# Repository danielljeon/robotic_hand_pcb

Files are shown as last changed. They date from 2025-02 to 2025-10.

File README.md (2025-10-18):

# robotic_hand_pcb



Robotic hand project for actuators/power electronics and sensors/instrumentation
university courses (PCB hardware).

STM32F446RE firmware
repo: [robotic_hand](https://github.com/danielljeon/robotic_hand).

- System architecture is explained in further detail in this software repo.

---

<details markdown="1">
  <summary>Table of Contents</summary>

<!-- TOC -->
* [robotic_hand_pcb](#robotic_hand_pcb)
  * [1 Overview](#1-overview)
  * [2 Board Specifications](#2-board-specifications)
    * [2.1 Connectors](#21-connectors)
      * [2.1.1 BAT+/VIN Terminals](#211-batvin-terminals)
    * [2.2 Switches & Jumpers](#22-switches--jumpers)
    * [2.3 Test Pads](#23-test-pads)
  * [3 Release Notes](#3-release-notes)
    * [3.1 v0.1.0](#31-v010)
    * [3.2 v0.2.0](#32-v020)
  * [4 Development Process](#4-development-process)
    * [4.1 Simulations: OrCAD X (PSpice)](#41-simulations-orcad-x-pspice)
    * [4.2 PCB Design: KiCad](#42-pcb-design-kicad)
    * [4.3 Firmware: CLion and STM32CubeMX](#43-firmware-clion-and-stm32cubemx)
    * [4.4. Version Control: GitHub](#44-version-control-github)
  * [5 Switching Buck Regulator](#5-switching-buck-regulator)
    * [5.1 Load Current Estimation](#51-load-current-estimation)
    * [5.2 Switching Frequency Selection](#52-switching-frequency-selection)
    * [5.3 Inductor Selection](#53-inductor-selection)
    * [5.4 Output Capacitor Selection](#54-output-capacitor-selection)
    * [5.5 Input Capacitor Selection](#55-input-capacitor-selection)
    * [5.6 PSpice Simulation](#56-pspice-simulation)
      * [5.6.1 Schematic](#561-schematic)
      * [5.6.2 Output](#562-output)
      * [5.6.3 Fast Fourier Transform (FFT)](#563-fast-fourier-transform-fft)
  * [💖 Sponsors](#-sponsors)
    * [PCBWay](#pcbway)
      * [Why PCBWay?](#why-pcbway)
<!-- TOC -->

</details>

---

<a href="https://www.pcbway.com">
  PCBWay Logo
</a>

This project is sponsored by **PCBWay**. You can learn more about their valuable
support here: [💖 Sponsors/PCBWay](#pcbway).

---

## 1 Overview

| Hand Assembly Back | Hand Assembly Front |
|:---:|:---:|
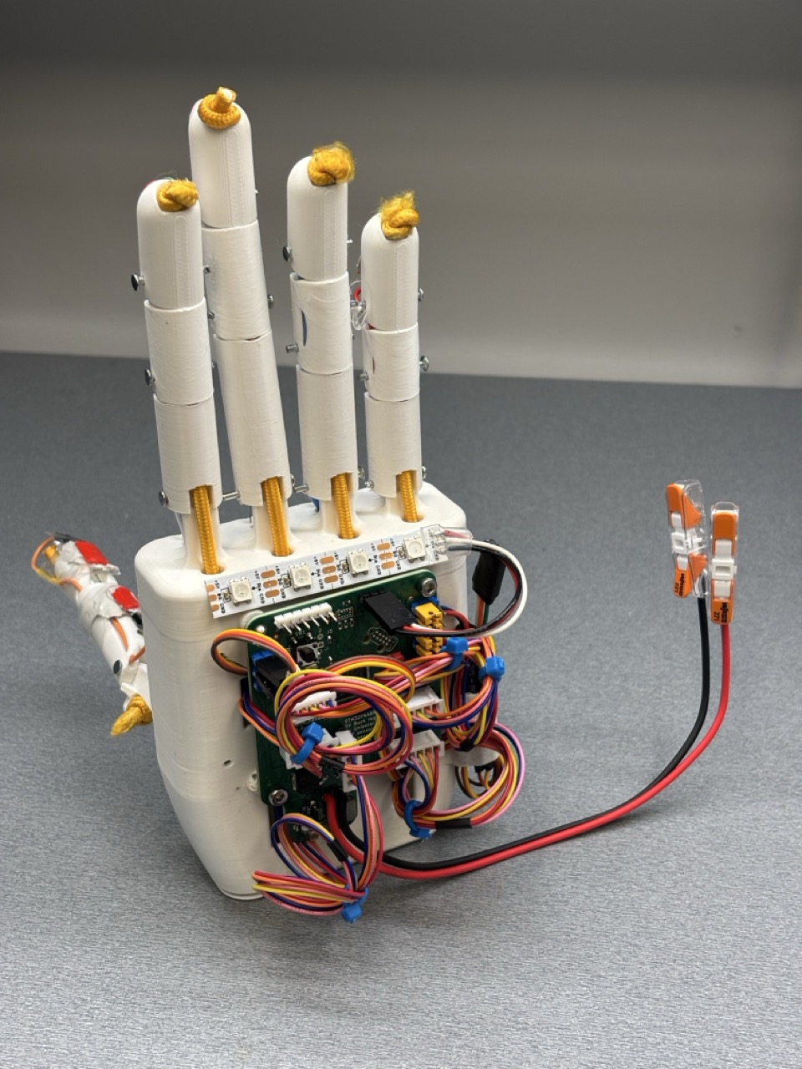
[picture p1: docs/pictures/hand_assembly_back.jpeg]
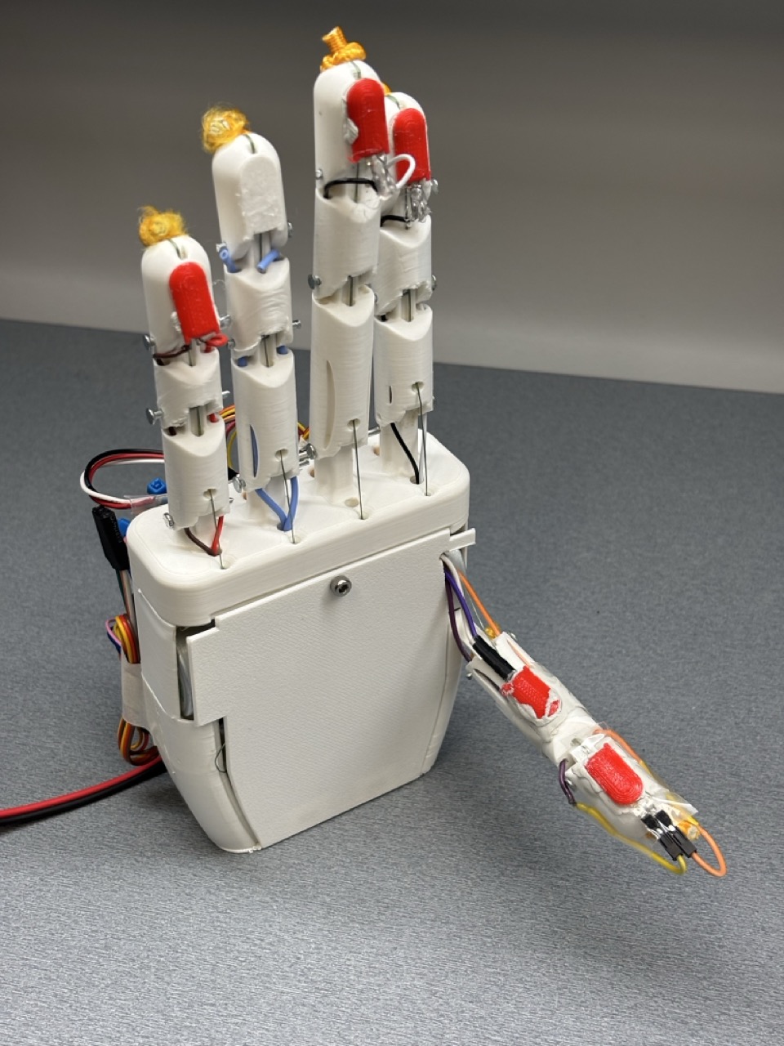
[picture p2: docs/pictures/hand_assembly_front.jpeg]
|  |  |

| Top | Bottom |
|:---:|:---:|
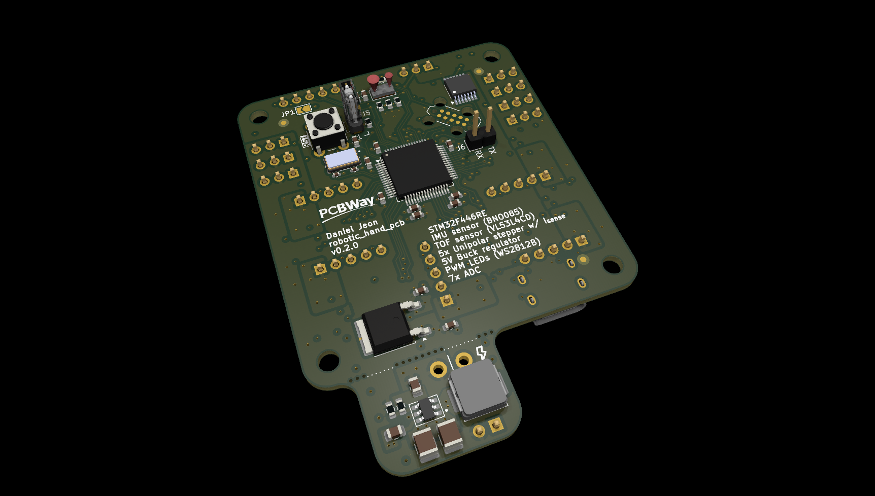
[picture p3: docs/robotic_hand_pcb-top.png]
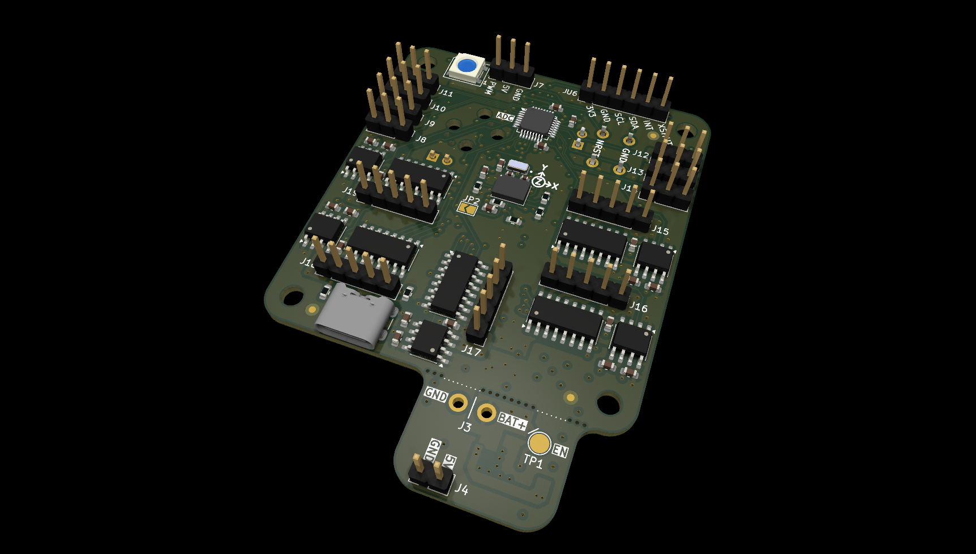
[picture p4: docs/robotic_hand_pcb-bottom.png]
|  |  |
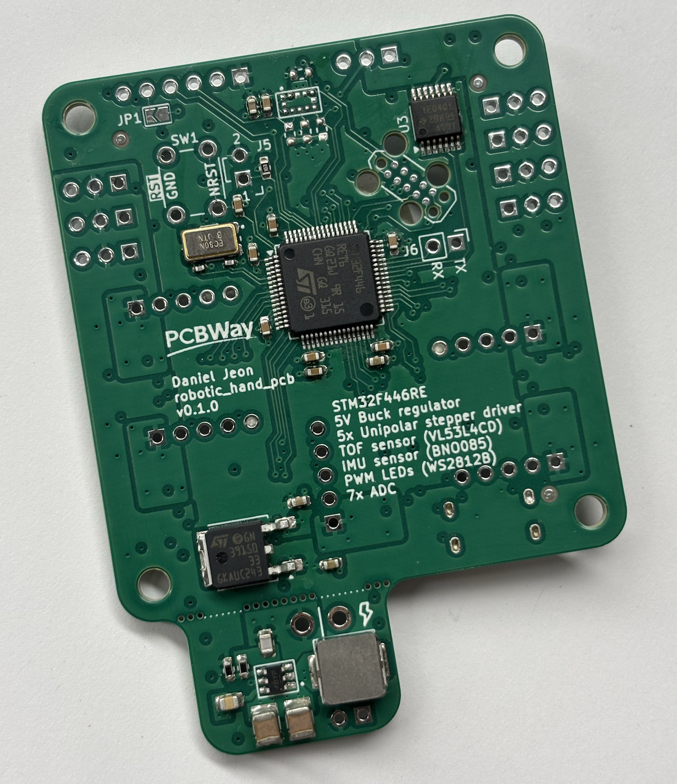
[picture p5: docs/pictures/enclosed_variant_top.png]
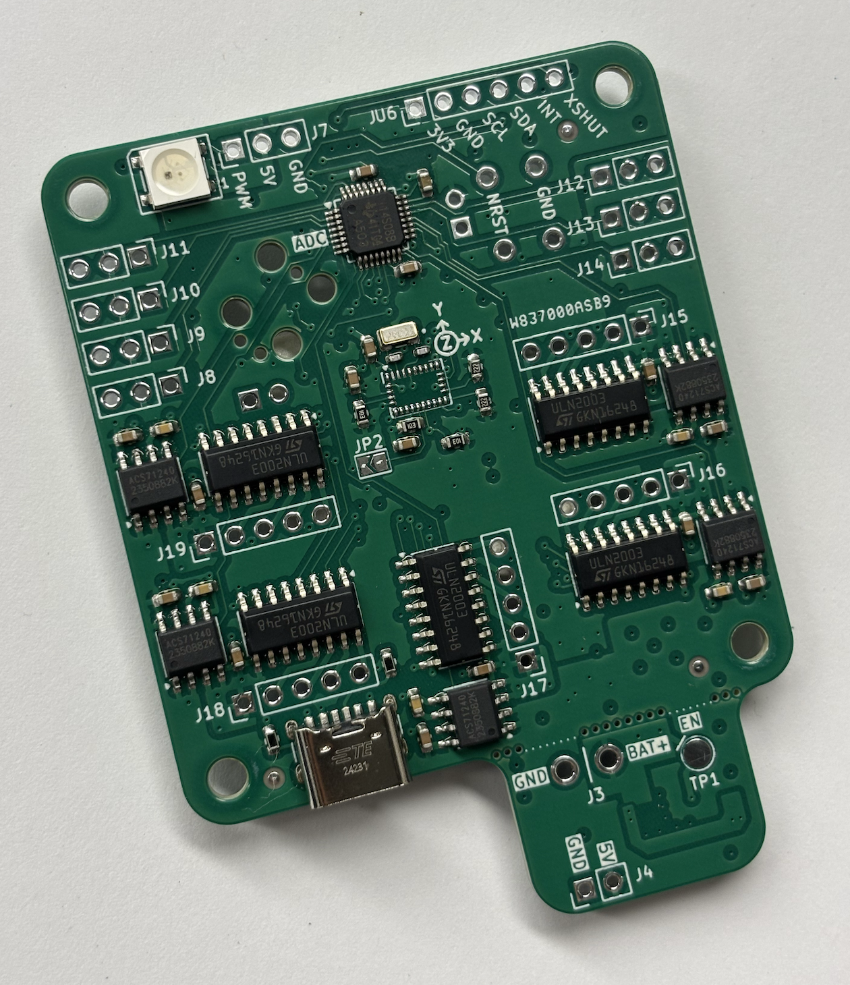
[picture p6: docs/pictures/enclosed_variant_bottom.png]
|  |  |

- Pictures show v0.1.0 production run.

---

## 2 Board Specifications

### 2.1 Connectors

| Connector |  Ref  | Description |
|---|:-----:|---|
| VL53L4CD Breakout  | (J)U6 | Breakout connector for TOF sensor |
| USB-C 5 V power |  J1 | Power only USB-C, primary 5 V source |
| Tag-Connect TC2050 |  J2 | Programming/debug connector |
| BAT+/VIN |  J3 | Pin 1: (GND) Ground, Pin 2: (BAT+) Power supply (> 5 V, <= 36 V), see [2.1.1 BAT+/VIN Terminals](#211-batvin-terminals). |
| 5V Breakout |  J4 | 5 V analog input 7 |
| BOOT0 jumper |  J5 | Open for run flash memory (pull-down on open) |
| UART Breakout |  J6 | General purpose UART breakout |
| WS2812B PWM LEDs |  J7 | 5 V Addressable LED breakout |
| ADC 1 |  J8 | 5 V analog input 1 |
| ADC 2 |  J9 | 5 V analog input 2 |
| ADC 3 |  J10  | 5 V analog input 3 |
| ADC 4 |  J11  | 5 V analog input 4 |
| ADC 5 |  J12  | 5 V analog input 5 |
| ADC 6 |  J13  | 5 V analog input 6 |
| ADC 7 |  J14  | 5 V analog input 7 |
| Unipolar Motor 1 |  J15  | Robotic finger 1 motor |
| Unipolar Motor 2 |  J16  | Robotic finger 2 motor |
| Unipolar Motor 3 |  J17  | Robotic finger 3 motor |
| Unipolar Motor 4 |  J18  | Robotic finger 4 motor |
| Unipolar Motor 5 |  J19  | Robotic finger 5 motor |

- All generic breakout connectors are standard 2.54 mm pitch Harwin connectors
  except for the BAT+/VIN connector.

#### 2.1.1 BAT+/VIN Terminals

The battery or supply terminals for the LMR51430 (5 V) buck regulator are custom
sizes designed for higher gauge wires.

The **recommended supply voltage is 12 V**, however the LMR51430 has a
theoretical range up to 36 volts.

- Hole: 1.5 mm diameter.
- Pad: 2.5 mm diameter.
- Pitch: 4 mm (center-to-center distance).

### 2.2 Switches & Jumpers

| Switch/Jumper | Ref | Description |
|---|:---:|---|
| MCU NRESET switch | SW1 | Generic 6 mm TH button, push to reset |
| VL53L4CD breakout INT | JP1 | Open = no breakout, closed = bridge breakout INT line |
| BNO085 clock select | JP2 | Open = crystal, closed = external/internal |

### 2.3 Test Pads

| Test Pad | Ref | Description |
|---|:---:|---|
| LMR51430 enable | TP1 | Buck converter enable pin (tied to VIN Battery supply by default) |

---

## 3 Release Notes

### 3.1 v0.1.0

- Production oriented 4-layer board variant.
    - Designed for single production run given course project requirement.
- Order date: 2025/02/23.
- Order number: `W837000ASB9`.

### 3.2 v0.2.0

- Updated PCB for hand reworks on `v0.1.0` to get full ADS114S08 feature
  functionality.
    - Requires software changes for this functionality, thus semantic versioning
      minor value was moved to `2`.
    - Rework shown in picture below:
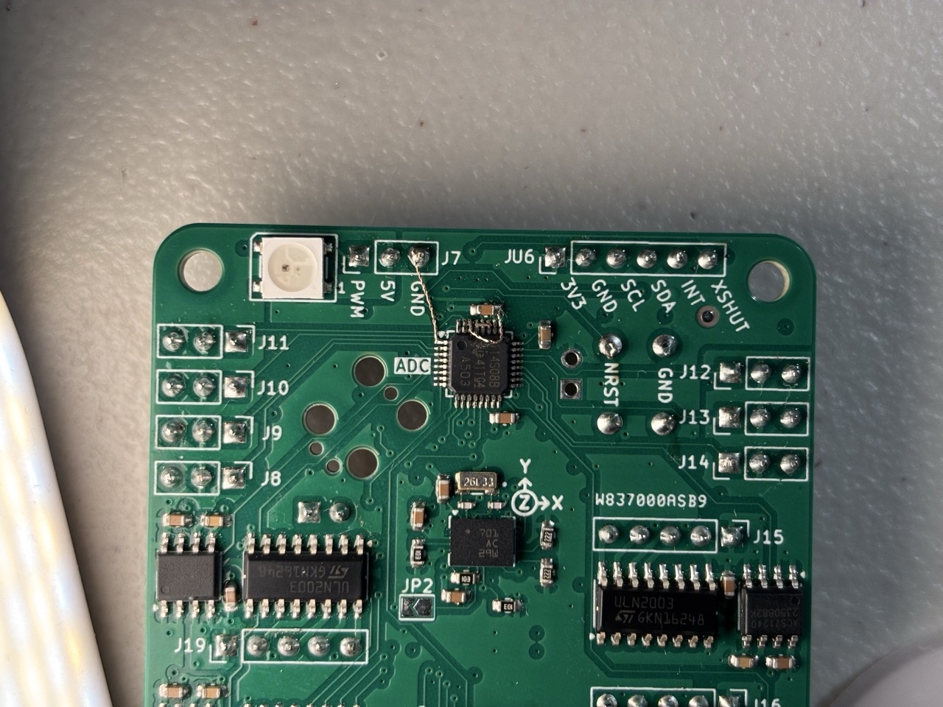
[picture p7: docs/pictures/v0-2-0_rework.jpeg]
      

---

## 4 Development Process

### 4.1 Simulations: OrCAD X (PSpice)

[OrCAD X (PSpice)](https://www.cadence.com/en_US/home/tools/pcb-design-and-analysis/analog-mixed-signal-simulation/pspice.html)
by Cadence was used for circuit simulation and evaluation.

Since this project relies heavily on Texas Instruments (TI) components (ADC ICs,
Darlington transistor arrays, and buck regulators), PSpice was chosen for design
verification and virtual testing. TI provides official PSpice models, making
simulations more accurate and reliable.

Initially, [PSpice for TI](https://www.ti.com/tool/PSPICE-FOR-TI) (a free
version limited to TI parts) was used. Upgrading to OrCAD X enabled full
compatibility and broader simulation capabilities.

### 4.2 PCB Design: KiCad

[KiCad](https://www.kicad.org/) was chosen for PCB design due to its ease of use
as a free, open-source software. Additionally, prior experience and personal
preference played a key role in the decision.

### 4.3 Firmware: CLion and STM32CubeMX

[CLion](https://www.jetbrains.com/clion/)
and [STM32CubeMX](https://www.st.com/en/development-tools/stm32cubemx.html) from
STMicroelectronics were selected based on prior experience and personal
preference. STM32CubeMX is utilized for initial component selection, pin
configuration, and HAL software generation, while CLion is used for general C
firmware development. For more details,
see [robotic_hand](https://github.com/danielljeon/robotic_hand).

### 4.4. Version Control: GitHub

[GitHub](https://github.com/) was chosen for its efficiency in version control
and support for Actions automations. These automations facilitated testing,
validation, and various manufacturing-related processes for both hardware and
software development.

---

## 5 Switching Buck Regulator

The LMR51430 was chosen for its wide input voltage range of 4.5 V to 36 V, high
output current of 3 A and overall efficiency.

> Datasheet: Datasheet: LMR51430 SLUSEF4A – JUNE 2022 – REVISED NOVEMBER 2022.

> Big thanks, as always, to the amazing publicly available resources online 👑:
> 1. [Switching Regulator PCB Design - Phil's Lab #60](https://www.youtube.com/watch?v=AmfLhT5SntE)
> 2. [Switching Regulator Component Selection & Sizing - Phil's Lab #71](https://www.youtube.com/watch?v=FqT_Ofd54fo)

### 5.1 Load Current Estimation

The expected current load is as follows:

| Load | Current | n |
|---|---|---|
| Motors + drivers  | 500 mA  | 5 |
| WS2812B LEDs | 60 mA | 1 |
| 3.3 V ICs via LDO | 100 mA  | 1 |

Approximate total current draw: 2660 mA = 2.66 A at 5 V.

In a real-world engineering scenario, current draw would be estimated using more
accurate models and measured across various revisions of development boards.
However, due to budget constraints and the need to support future higher-voltage
applications, a 3 A buck regulator was chosen, as it is a commonly available and
cost-effective option.

While this provides only an 11% safety margin, it was deemed acceptable for
early research and educational purposes. In the worst-case scenario, the board
can also be powered by an external 5 V power supply if needed.

### 5.2 Switching Frequency Selection

The LMR51430 is capable of 500 kHz and 1.1 MHz switching. The design opted for
the 500 kHz configuration for reduced switching noise and its application of
motor current driving. A lower switching frequency would theoretically reduce
switching losses and improve efficiency at high current draw.

### 5.3 Inductor Selection

The following calculations are based on the recommendations provided in the
LMR51430 datasheet.

The desired peak-to-peak ripple current is given by the following:

$$\Delta i_L = \frac{V_{OUT} \times \left( V_{IN \space MAX} - V_{OUT} \right)}{V_{IN \space MAX} \times L \times f_{SW}}$$

- $L$ = Inductance driving ripple.

The minimum inductor specification is given by:

$$L_{min} = \frac{V_{\text{IN MAX}} - V_{\text{OUT}}}{I_{\text{OUT}} \times K_{\text{IND}}} \times \frac{V_{\text{OUT}}}{V_{\text{IN MAX}} \times f_{\text{SW}}}$$
$$L_{min} = \frac{12 \space \text{V} - 5 \space \text{V}}{3 \space \text{A} \times 0.3} \times \frac{5 \space \text{V}}{12 \space \text{V} \times 500 \times 10^{3} \space \text{Hz}}$$
$$L_{min} = 6.84 \times 10^{-6} \space \text{H} = 6.84 \space \mathrm{\mu H}$$

- $K_{IND}$ = Coefficient representing the inductor ripple current as a fraction
  of the maximum output current, utilizing 0.3 for this project.
    - > A reasonable value of KIND must be 20% to 60% of maximum IOUT supported
      > by the converter.
      >
      > - Datasheet section: _9.2.2.4 Inductor Selection_.
- $f_{\text{SW}}$ = Switching frequency, 500 kHz chosen.
- $V_{\text{IN MAX}}$ = Input voltage, expected 12 V with ±1 V, 13 V.
- $V_{\text{OUT}}$ = Output voltage, 5 V.
- $I_{\text{OUT}}$ = Output current, approximately 3 A.

> During an instantaneous over-current operation event, the RMS and peak
> inductor current can be high. The inductor saturation current must be higher
> than peak current limit level.
>
> In general, choose lower inductance in switching power supplies because it
> usually corresponds to faster transient response, smaller DCR, and reduced
> size for more compact designs. Too low of an inductance can generate too large
> of an inductor current ripple such that over-current protection at the full
> load can be falsely triggered and generates more inductor core loss because
> the current ripple is larger. Larger inductor current ripple also implies
> larger output voltage ripple with the same output capacitors. With peak
> current mode control,ensure there is an adequate amount of inductor ripple
> current. A larger inductor ripple current improves the comparator
> signal-to-noise ratio.
>
> - Datasheet section: _9.2.2.4 Inductor Selection_.

The final minimum inductance value of 6.84 μH closely matches the example
application values provided for a 12V input and 5V output, which uses 6.8 μH.

### 5.4 Output Capacitor Selection

> Minimize the output capacitance to keep cost and size down. The output
> capacitor or capacitors, COUT, must be chosen with care because it directly
> affects the steady state output voltage ripple, loop stability, and output
> voltage overshoot and undershoot during load current transient. The output
> voltage ripple is essentially composed of two parts. One part is caused by the
> inductor ripple current flowing through the Equivalent Series Resistance (ESR)
> of the output capacitors ... The other part is caused by the inductor current
> ripple charging and discharging the output capacitors.
>
> - Datasheet section: _9.2.2.5 Output Capacitor Selection_.

Inductor current ripple flowing through the ESR is given by:

$$\Delta V_{\text{OUT ESR}} = \Delta i_L \times \text{ESR} = K_{\text{IND}} \times I_{\text{OUT}} \times \text{ESR}$$

Inductor current ripple charging and discharging the output capacitors is given
by:

$$\Delta V_{\text{OUT C}} = \frac{\Delta i_L}{8 \times f_{\text{SW}} \times C_{\text{OUT}}} = \frac{K_{\text{IND}} \times I_{\text{OUT}}}{8 \times f_{\text{SW}} \times C_{\text{OUT}}}$$

- $K_{\text{IND}}$ = target ripple ratio of the inductor
  current ($\Delta i L / I_{\text{OUT}}$).

The minimum output capacitance needed for a specified output voltage overshoot
and undershoot is given by:

$$C_{\text{OUT}} > \frac{1}{2} \times \frac{8 \times (I_{\text{OH}} - I_{\text{OL}})}{f_{\text{SW}} \times \Delta V_{\text{OUT SHOOT}}}$$

- $I_{\text{OL}}$ = low level output current during load transient.
- $I_{\text{OH}}$ = high level output current during load transient.
- $V_{\text{OUT SHOOT}}$ = target output voltage overshoot or undershoot.

For this project a target output ripple is arbitrarily set for 30 mV and the
ripple ratio of inductor current is set to 0.3.

- $\Delta V_{\text{OUT ESR}} = \Delta V_{\text{OUT C}} = 30 mV$
- $K_{\text{IND}} = 0.3$

This yields ESR < 75 mΩ and output capacitance > 14 μF.

### 5.5 Input Capacitor Selection

> The LMR51430 device requires a high frequency input decoupling capacitor or
> capacitor. The typical recommended value for the high frequency decoupling
> capacitor is 4.7 μF or higher. TI recommends a high-quality ceramic type X5R
> or X7R with a sufficient voltage rating. The voltage rating must be greater
> than the maximum input voltage. To compensate the derating of ceramic
> capacitors, TI recommends a voltage rating of twice the maximum input voltage.
>
> - Datasheet section: _9.2.2.5 Output Capacitor Selection_.

### 5.6 PSpice Simulation

Due to the limited availability of publicly accessible PSpice models, the
LMR51420 model was used instead. Based on datasheet specifications, the 2A
variant of the LMR514x0 series appears largely similar, with the primary
difference being the requirement for a 10 μH inductor.

#### 5.6.1 Schematic

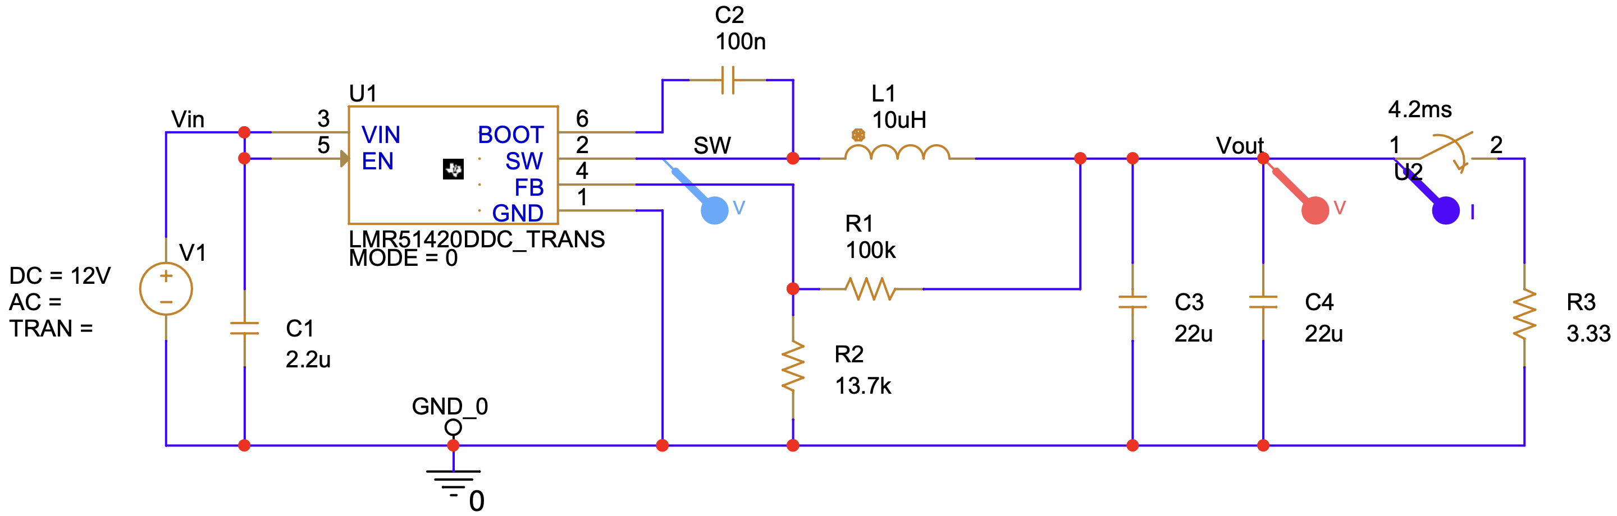
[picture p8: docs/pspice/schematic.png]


To simulate sudden current loads, a 3.3 Ω load (drawing 1.5 A at 5 V) is added
and set to switch at 4.2 ms. The switch has a transition time of 15 μs.

#### 5.6.2 Output

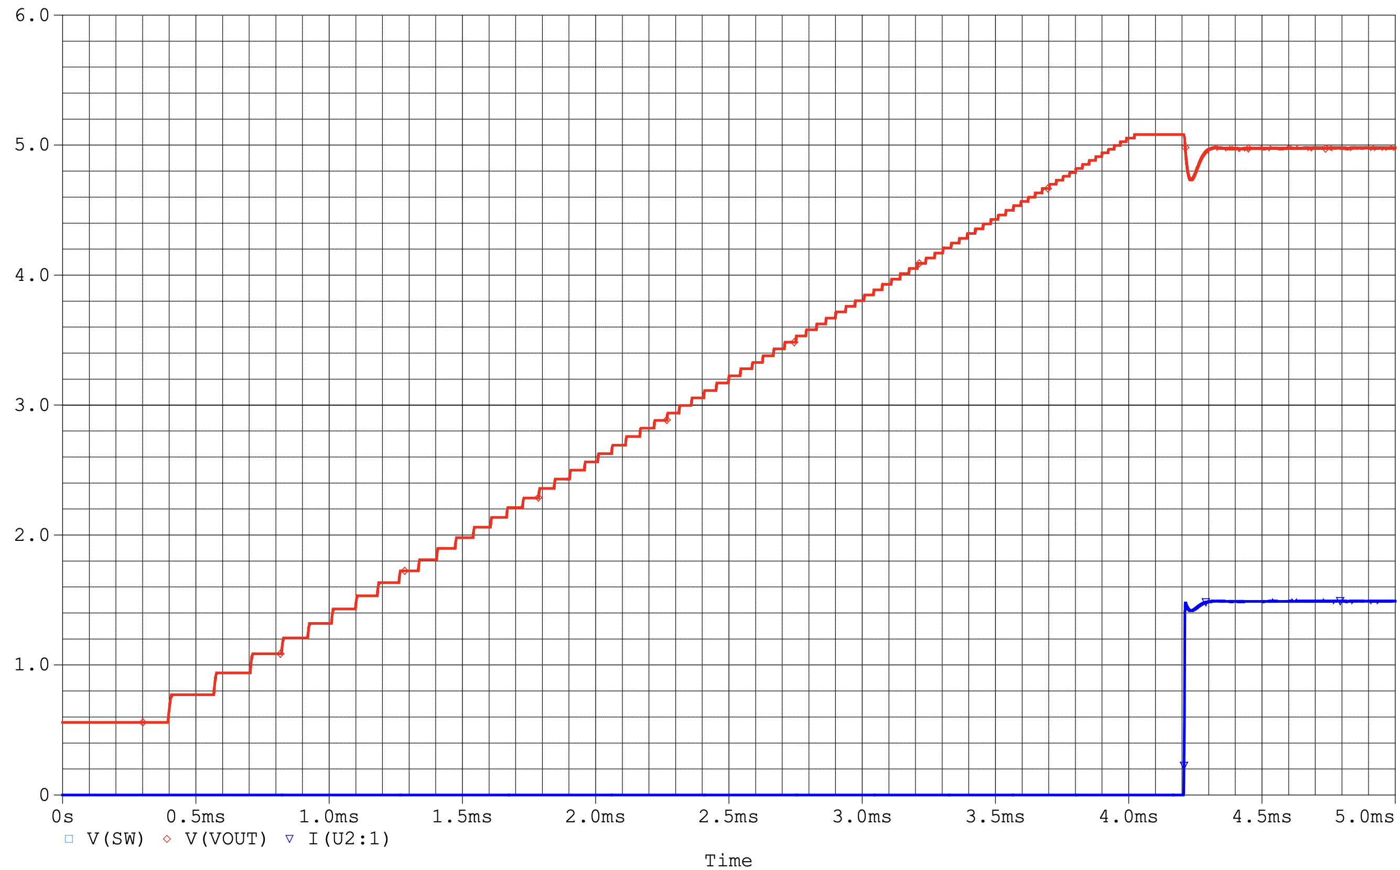
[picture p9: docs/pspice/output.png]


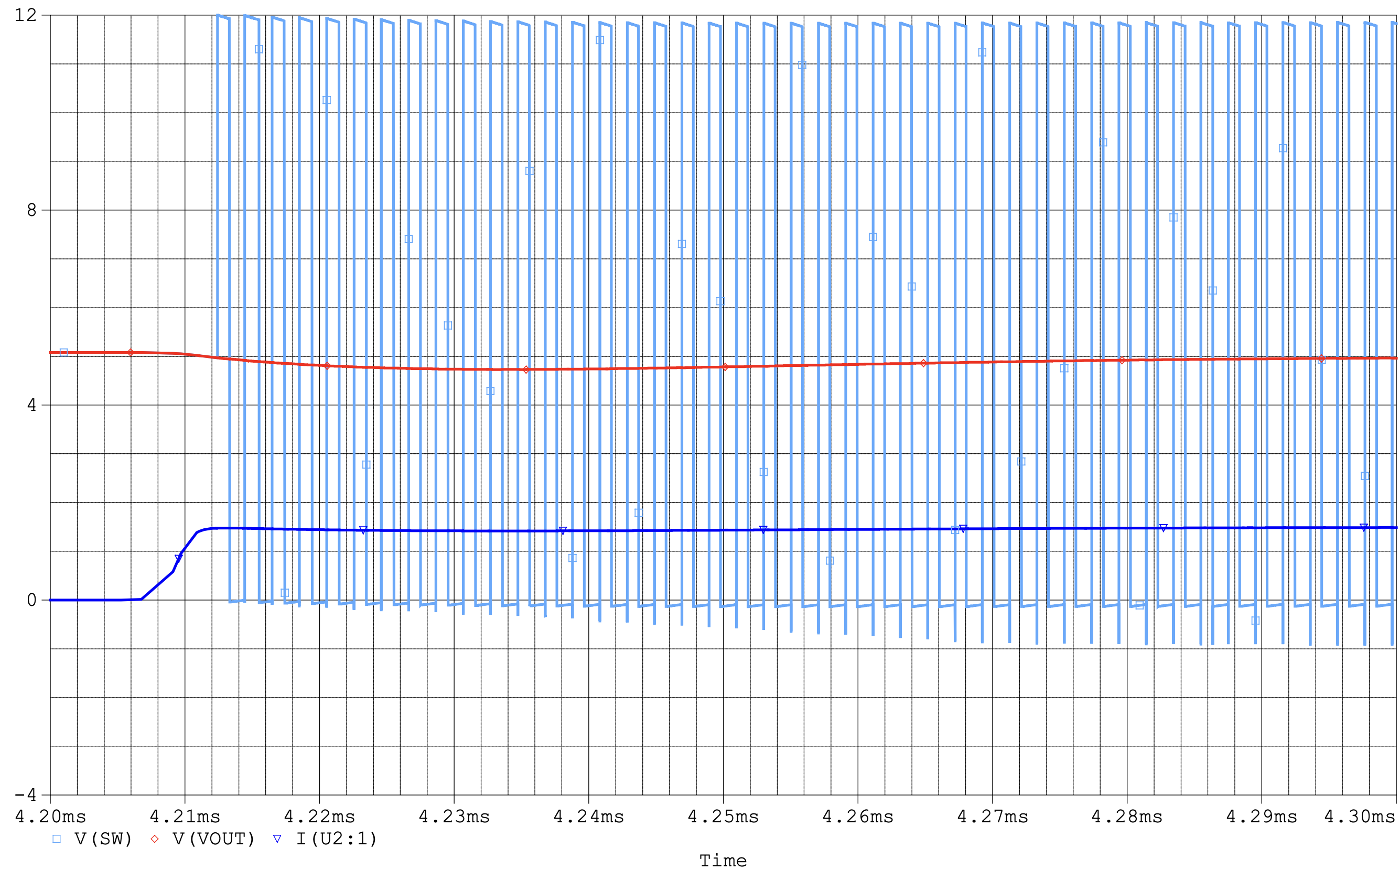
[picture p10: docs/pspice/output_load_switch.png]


#### 5.6.3 Fast Fourier Transform (FFT)

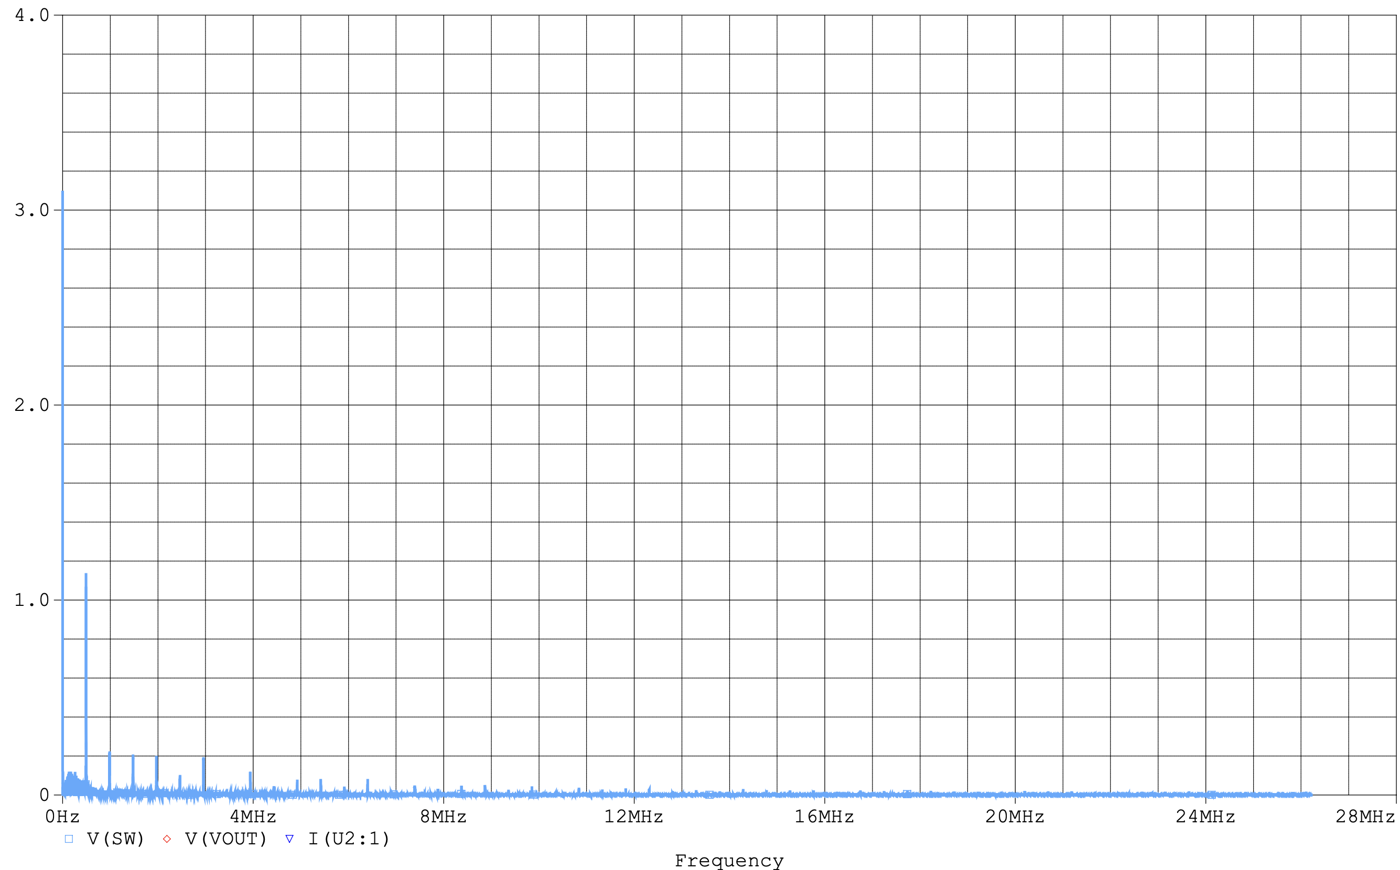
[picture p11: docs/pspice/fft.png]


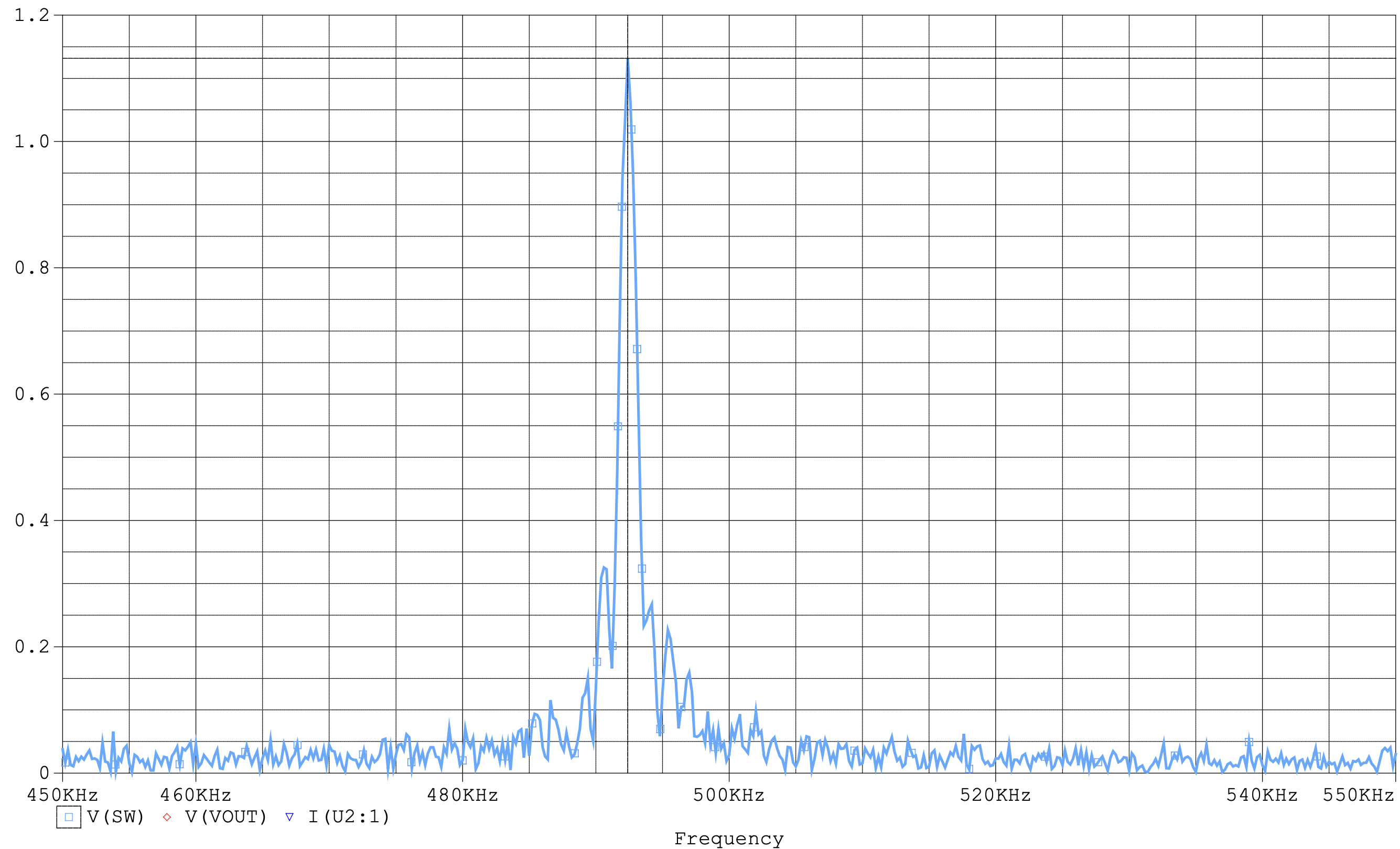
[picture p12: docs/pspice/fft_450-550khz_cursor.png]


For this simulation run, the fundamental frequency was found to be 492.400 kHz
with a resultant amplitude of 1.1316. Due to the short simulation duration, the
time required to ramp up to the final voltage, and the handling of sudden loads,
it is hypothesized that the FFT results deviate slightly from the expected 500
kHz.

---

## 💖 Sponsors

### PCBWay

<a href="https://www.pcbway.com">
  PCBWay Logo
</a>

This project is sponsored by [**PCBWay**](https://www.pcbway.com), whose PCB
manufacturing services are essential in producing high-quality prototypes for
its development. Their support ensures reliable boards that meet the project's
demands.

#### Why PCBWay?

PCBWay stands out for their exceptional services and commitment to the
community:

- **PCB Manufacturing**: High-quality fabrication with options for multilayer,
  rigid-flex, and advanced designs.
- **PCB Assembly**: Comprehensive solutions, including soldering, component
  sourcing, and assembly.
- **CNC Machining & 3D Printing**: Additional prototyping options to support
  complete product development.
- **Fast Turnaround**: Reliable and quick production times to keep projects on
  schedule.
- **Support for Open Source & Education**: PCBWay actively sponsors projects and
  provides educational resources like tutorials, videos, and documentation,
  empowering developers and hobbyists.
    - This commitment to education and open-source advocacy was a key factor in
      choosing them as a partner 🙂.

Their dedication to professional-grade services and fostering innovation makes
PCBWay an invaluable partner in bringing this project to life.

Learn more here: [Why PCBWay?](https://www.pcbway.com/why.html)

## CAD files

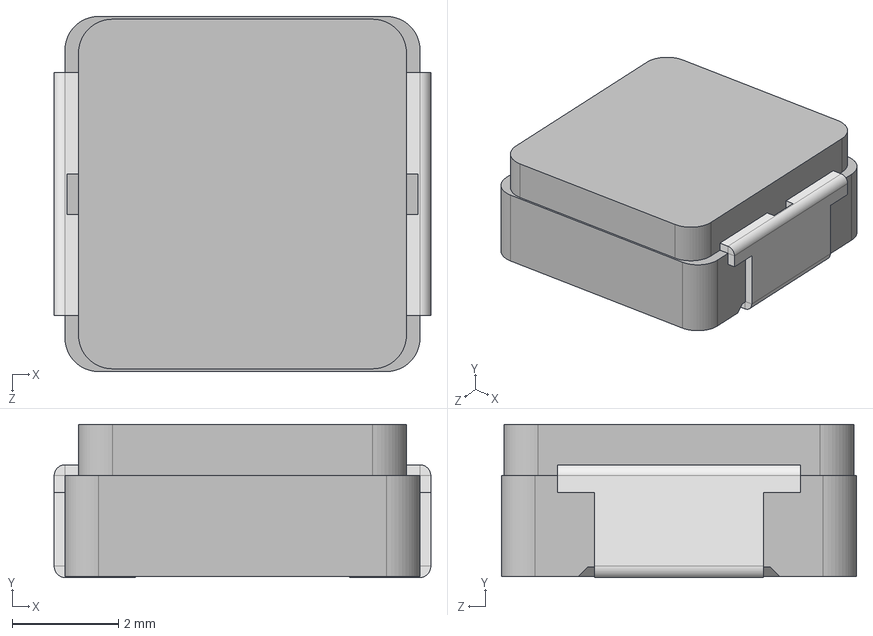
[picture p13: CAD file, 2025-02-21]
component_local/model_3d/IHLP2525CZ.step
7.08 x 2.88 x 6.67 mm

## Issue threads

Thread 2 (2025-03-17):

ADS114S08 missing smoothing resistors

danielljeon, 2025-03-17:
# ADS114S08 missing smoothing resistors

The current ADS114S08 schematic fails to meet datasheet recommendations "**10.1.1 Serial Interface Connections**".

> "Place 47-Ω resistors in series with all digital input and output pins (CS, SCLK, DIN, DOUT/DRDY, and DRDY). This resistance smooths sharp transitions, suppresses overshoot, and offers some overvoltage protection. Care must be taken to meet all SPI timing requirements because the additional resistors interact with the bus capacitances present on the digital signal lines."

47 Ω resistors should be in series with the following:

1. RESET_N
2. DRDY_N
3. DOUT/DRDY_N
4. SCLK
5. DIN
6. CS
7. START/SYNC

This PCB was originally intended for a single production run, so it is unlikely to be directly resolved beyond documentation. Future designs should address and correct this issue.

A note has been left on the schematic to document the known issue.

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

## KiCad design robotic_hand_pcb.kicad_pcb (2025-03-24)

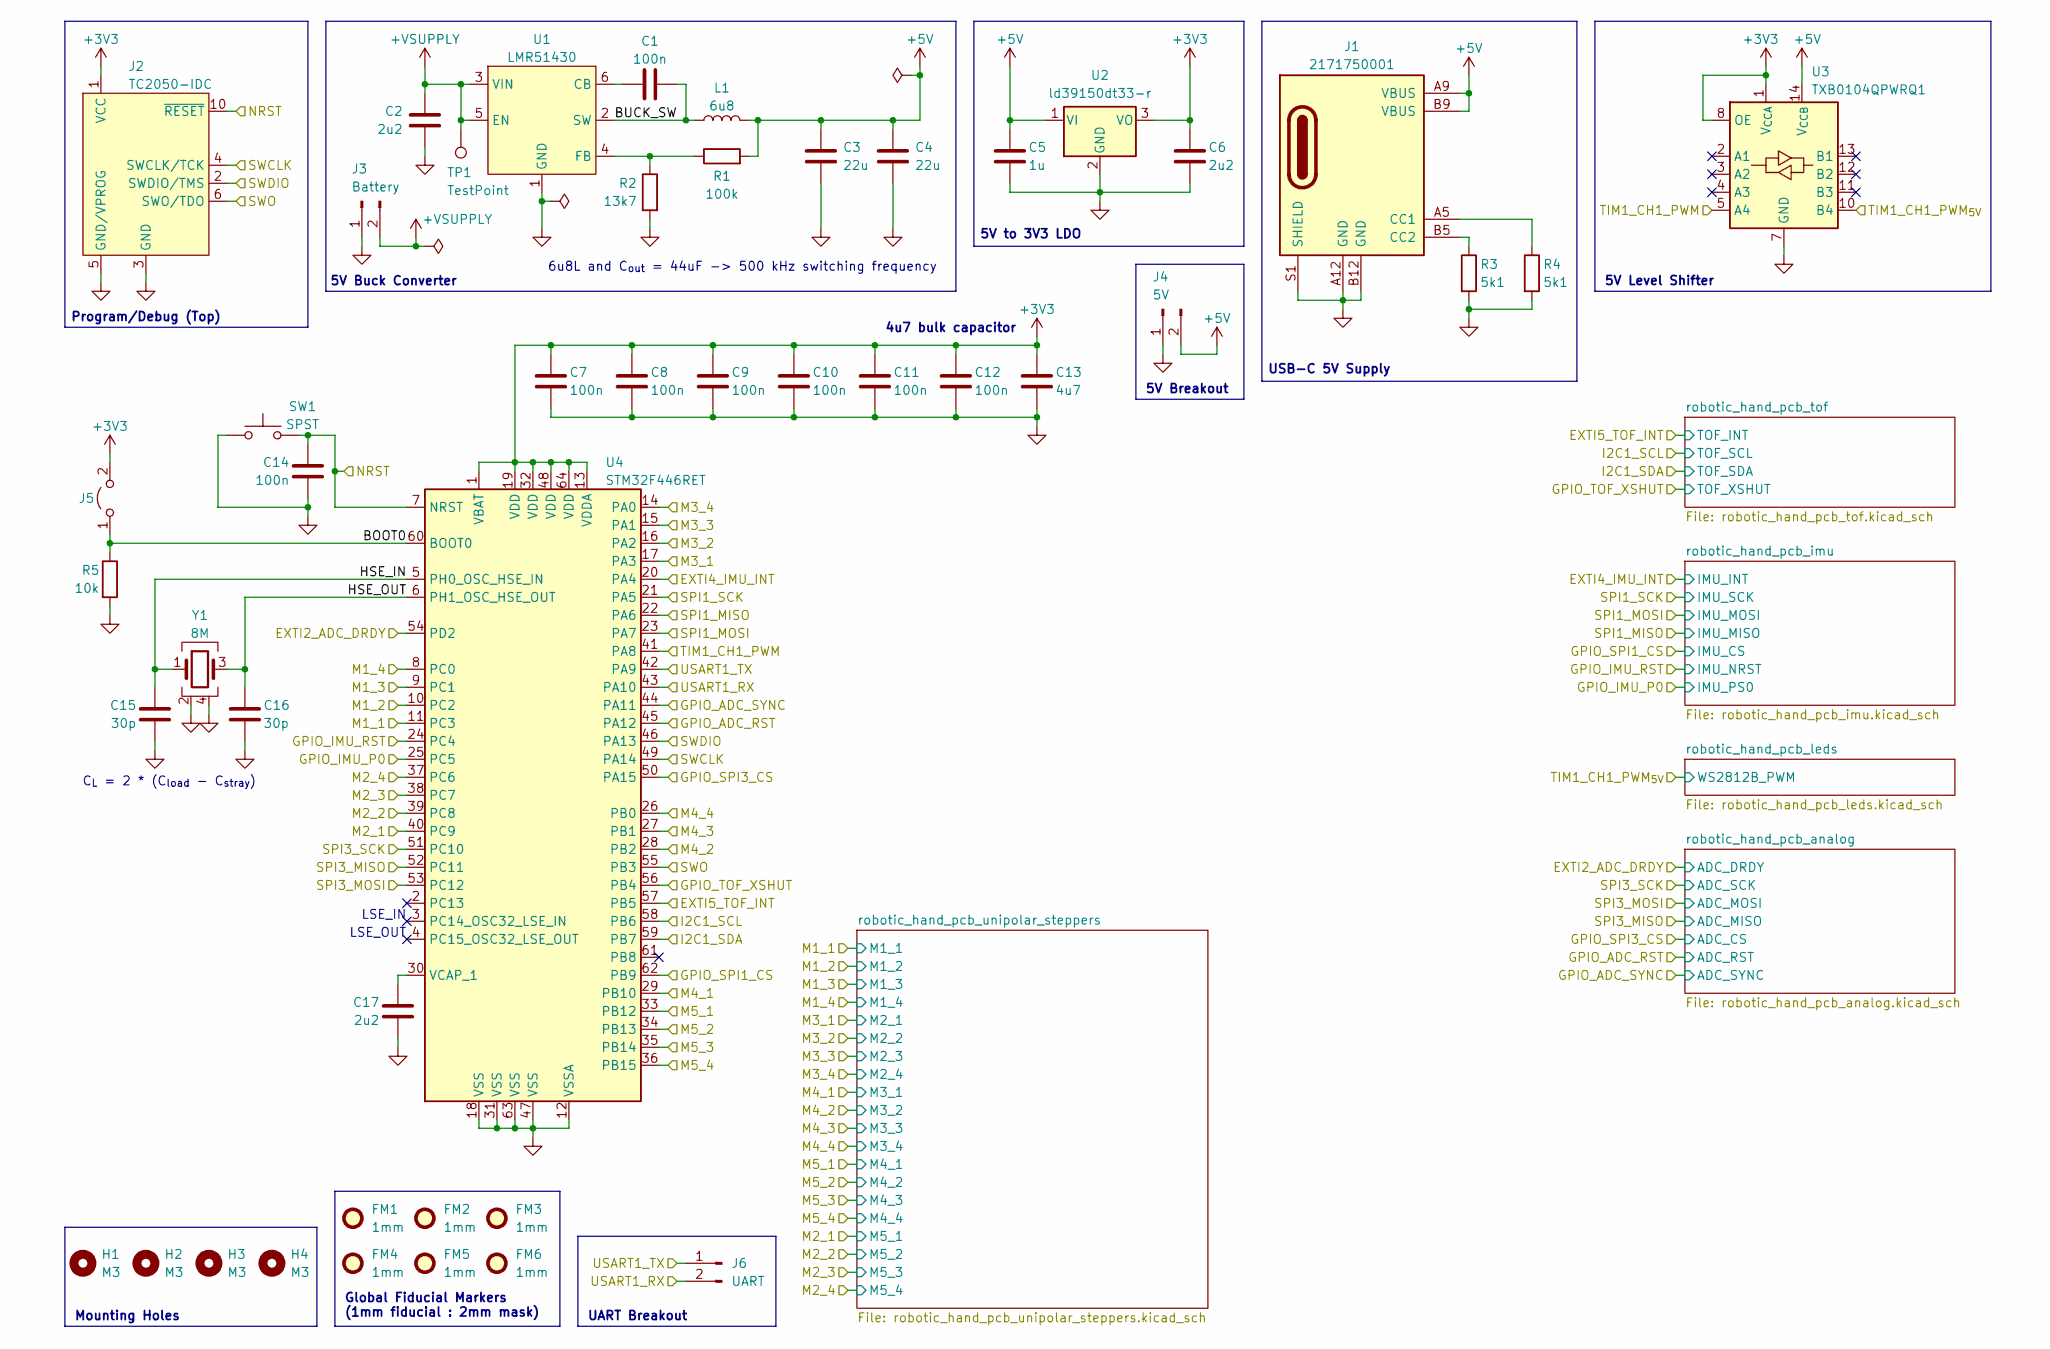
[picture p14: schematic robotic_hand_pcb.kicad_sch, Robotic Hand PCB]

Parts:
C1: 100n; C_0805_2012Metric
C2: 2u2; C_0805_2012Metric
C3, C4: 22u; C_1210_3225Metric
C5: 1u; C_0603_1608Metric
C6, C17: 2u2; C_0603_1608Metric
C7, C8, C9, C10, C11, C12, C14: 100n; C_0603_1608Metric
C13: 4u7; C_0603_1608Metric
C15, C16: 30p; C_0402_1005Metric
FM1, FM2, FM3, FM4, FM5, FM6: 1mm; Fiducial_1mm_Mask2mm
H1, H2, H3, H4: M3; MountingHole_3.2mm_M3
J1: 2171750001; molex_2171750001_usb_c_6p; Manufacturer Part Number 2171750001
J2: TC2050-IDC; tag_connect_tc2050-idc; Manufacturer Part Number TC2050-IDC
J3: Battery; battery
J4: 5V; PinHeader_1x02_P2.54mm_Vertical
J5: harwin_2p_2-54_jumper_open; Manufacturer Part Number M20-9990246
J6: UART; PinHeader_1x02_P2.54mm_Vertical
L1: 6u8; vishay_ihlp-2525cz
R1: 100k; R_0603_1608Metric
R2: 13k7; R_0603_1608Metric
R3, R4: 5k1; R_0603_1608Metric
R5: 10k; R_0603_1608Metric
SW1: SPST; SW_PUSH_6mm
TP1: TestPoint; TestPoint_Pad_D2.5mm
U1: LMR51430; lmr51430; Manufacturer Part Number LMR51430
U2: ld39150dt33-r; to-252-2_dpak-2-leg; Manufacturer Part Number LD39150DT33-R
U3: TXB0104QPWRQ1; txb0104qpwrq1; Manufacturer Part Number TXB0104QPWRQ1
U4: STM32F446RET; LQFP-64_10x10mm_P0.5mm; Manufacturer Part Number STM32F446RE
Y1: 8M; ecs_ecx-64; Manufacturer Part Number ECS-80-18-23B-JTN-TR

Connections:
+3V3: C6.1, C7.1, C8.1, C9.1, C10.1, C11.1, C12.1, C13.1, J2.1 (VCC), J5.2, U2.3 (VO), U3.1 (V_{CCA}), U3.8 (OE), U4.1 (VBAT), U4.13 (VDDA), U4.19 (VDD), U4.32 (VDD), U4.48 (VDD), U4.64 (VDD); also elsewhere on the board
+5V: C3.2, C4.2, C5.1, J1.A9 (VBUS), J1.B9 (VBUS), J4.2, L1.2, R1.2, U2.1 (VI), U3.14 (V_{CCB}); also elsewhere on the board
+VSUPPLY: C2.1, J3.2, TP1.1, U1.3 (VIN), U1.5 (EN)
/BOOT0: J5.1, R5.1, U4.60 (BOOT0)
/BUCK_SW: C1.2, L1.1, U1.2 (SW)
/EXTI2_ADC_DRDY: U4.54 (PD2); also elsewhere on the board
/EXTI4_IMU_INT: U4.20 (PA4); also elsewhere on the board
/EXTI5_TOF_INT: U4.57 (PB5); also elsewhere on the board
/GPIO_ADC_RST: U4.45 (PA12); also elsewhere on the board
/GPIO_ADC_SYNC: U4.44 (PA11); also elsewhere on the board
/GPIO_IMU_P0: U4.25 (PC5); also elsewhere on the board
/GPIO_IMU_RST: U4.24 (PC4); also elsewhere on the board
/GPIO_SPI1_CS: U4.62 (PB9); also elsewhere on the board
/GPIO_SPI3_CS: U4.50 (PA15); also elsewhere on the board
/GPIO_TOF_XSHUT: U4.56 (PB4); also elsewhere on the board
/HSE_IN: C15.1, U4.5 (PH0_OSC_HSE_IN), Y1.1
/HSE_OUT: C16.1, U4.6 (PH1_OSC_HSE_OUT), Y1.3
/I2C1_SCL: U4.58 (PB6); also elsewhere on the board
/I2C1_SDA: U4.59 (PB7); also elsewhere on the board
/M1_1: U4.11 (PC3); also elsewhere on the board
/M1_2: U4.10 (PC2); also elsewhere on the board
/M1_3: U4.9 (PC1); also elsewhere on the board
/M1_4: U4.8 (PC0); also elsewhere on the board
/M2_1: U4.40 (PC9); also elsewhere on the board
/M2_2: U4.39 (PC8); also elsewhere on the board
/M2_3: U4.38 (PC7); also elsewhere on the board
/M2_4: U4.37 (PC6); also elsewhere on the board
/M3_1: U4.17 (PA3); also elsewhere on the board
/M3_2: U4.16 (PA2); also elsewhere on the board
/M3_3: U4.15 (PA1); also elsewhere on the board
/M3_4: U4.14 (PA0); also elsewhere on the board
/M4_1: U4.29 (PB10); also elsewhere on the board
/M4_2: U4.28 (PB2); also elsewhere on the board
/M4_3: U4.27 (PB1); also elsewhere on the board
/M4_4: U4.26 (PB0); also elsewhere on the board
/M5_1: U4.33 (PB12); also elsewhere on the board
/M5_2: U4.34 (PB13); also elsewhere on the board
/M5_3: U4.35 (PB14); also elsewhere on the board
/M5_4: U4.36 (PB15); also elsewhere on the board
/NRST: C14.2, J2.10 (~RESET), SW1.2, U4.7 (NRST)
/SPI1_MISO: U4.22 (PA6); also elsewhere on the board
/SPI1_MOSI: U4.23 (PA7); also elsewhere on the board
/SPI1_SCK: U4.21 (PA5); also elsewhere on the board
/SPI3_MISO: U4.52 (PC11); also elsewhere on the board
/SPI3_MOSI: U4.53 (PC12); also elsewhere on the board
/SPI3_SCK: U4.51 (PC10); also elsewhere on the board
/SWCLK: J2.4 (SWCLK/TCK), U4.49 (PA14)
/SWDIO: J2.2 (SWDIO/TMS), U4.46 (PA13)
/SWO: J2.6 (SWO/TDO), U4.55 (PB3)
/TIM1_CH1_PWM: U3.5 (A4), U4.41 (PA8)
/TIM1_CH1_PWM_{5V}: U3.10 (B4); also elsewhere on the board
/USART1_RX: J6.2, U4.43 (PA10)
/USART1_TX: J6.1, U4.42 (PA9)
GND: C2.2, C3.1, C4.1, C5.2, C6.2, C7.2, C8.2, C9.2, C10.2, C11.2, C12.2, C13.2, C14.1, C15.2, C16.2, C17.2, J1.A12 (GND), J1.B12 (GND), J1.S1 (SHIELD), J2.3 (GND), J2.5 (GND/VPROG), J3.1, J4.1, R2.2, R3.2, R4.2, R5.2, SW1.1, U1.1 (GND), U2.2 (GND), U3.7 (GND), U4.12 (VSSA), U4.18 (VSS), U4.31 (VSS), U4.47 (VSS), U4.63 (VSS), Y1.2, Y1.4; also elsewhere on the board
unnamed: J1.A5 (CC1), R4.1
unnamed: J1.B5 (CC2), R3.1
unnamed: C1.1, U1.6 (CB)
unnamed: R1.1, R2.1, U1.4 (FB)
unnamed: C17.1, U4.30 (VCAP_1)

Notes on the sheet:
LSE_OUT
5V Buck Converter
5V Breakout
4u7 bulk capacitor
Program/Debug (Top)
UART Breakout
Global Fiducial Markers (1mm fiducial : 2mm mask)
C_{L} = 2 * (C_{load} - C_{stray})
USB-C 5V Supply
LSE_IN
Mounting Holes
5V Level Shifter
6u8L and C_{out} = 44uF -> 500 kHz switching frequency
5V to 3V3 LDO

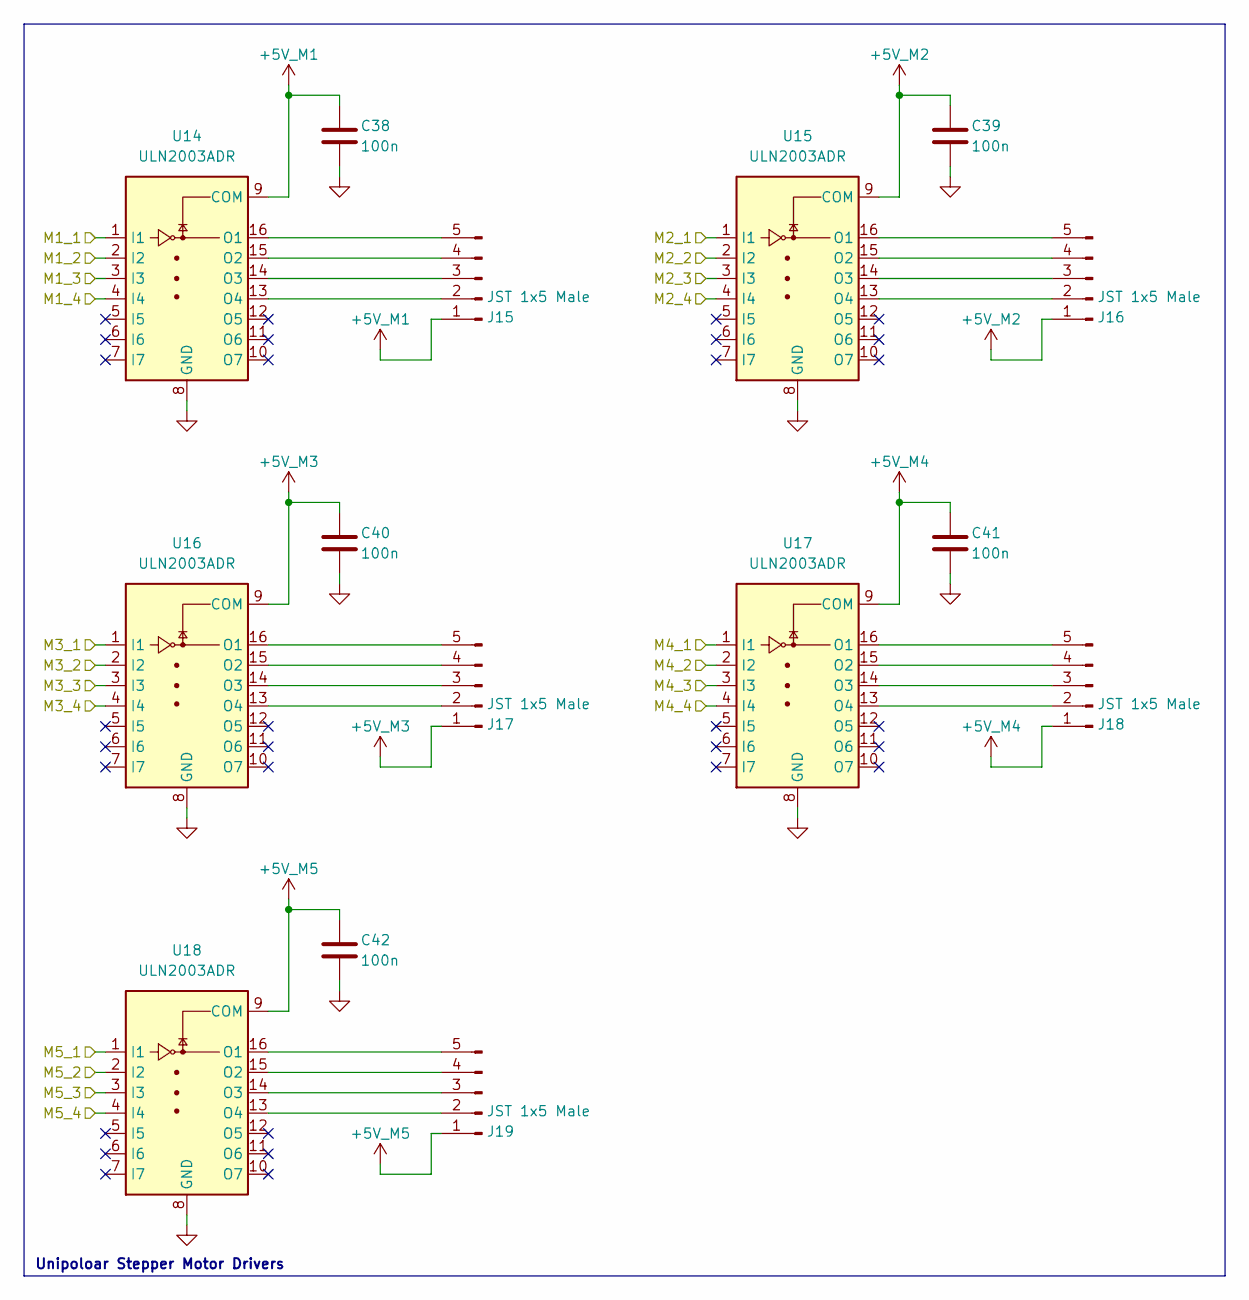
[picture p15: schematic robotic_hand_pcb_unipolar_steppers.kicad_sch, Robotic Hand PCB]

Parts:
C38, C39, C40, C41, C42: 100n; C_0603_1608Metric
J15, J16, J17, J18, J19: JST 1x5 Male; PinHeader_1x05_P2.54mm_Vertical
U14, U15, U16, U17, U18: ULN2003ADR; SOIC-16_3.9x9.9mm_P1.27mm

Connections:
+5V_M1: C38.1, J15.1, U14.9 (COM); also elsewhere on the board
+5V_M2: C39.1, J16.1, U15.9 (COM); also elsewhere on the board
+5V_M3: C40.1, J17.1, U16.9 (COM); also elsewhere on the board
+5V_M4: C41.1, J18.1, U17.9 (COM); also elsewhere on the board
+5V_M5: C42.1, J19.1, U18.9 (COM); also elsewhere on the board
/M1_1: U14.1 (I1); also elsewhere on the board
/M1_2: U14.2 (I2); also elsewhere on the board
/M1_3: U14.3 (I3); also elsewhere on the board
/M1_4: U14.4 (I4); also elsewhere on the board
/M2_1: U18.1 (I1); also elsewhere on the board
/M2_2: U18.2 (I2); also elsewhere on the board
/M2_3: U18.3 (I3); also elsewhere on the board
/M2_4: U18.4 (I4); also elsewhere on the board
/M3_1: U15.1 (I1); also elsewhere on the board
/M3_2: U15.2 (I2); also elsewhere on the board
/M3_3: U15.3 (I3); also elsewhere on the board
/M3_4: U15.4 (I4); also elsewhere on the board
/M4_1: U16.1 (I1); also elsewhere on the board
/M4_2: U16.2 (I2); also elsewhere on the board
/M4_3: U16.3 (I3); also elsewhere on the board
/M4_4: U16.4 (I4); also elsewhere on the board
/M5_1: U17.1 (I1); also elsewhere on the board
/M5_2: U17.2 (I2); also elsewhere on the board
/M5_3: U17.3 (I3); also elsewhere on the board
/M5_4: U17.4 (I4); also elsewhere on the board
GND: C38.2, C39.2, C40.2, C41.2, C42.2, U14.8 (GND), U15.8 (GND), U16.8 (GND), U17.8 (GND), U18.8 (GND); also elsewhere on the board
unnamed: J15.2, U14.13 (O4)
unnamed: J15.3, U14.14 (O3)
unnamed: J15.4, U14.15 (O2)
unnamed: J15.5, U14.16 (O1)
unnamed: J16.2, U15.13 (O4)
unnamed: J16.3, U15.14 (O3)
unnamed: J16.4, U15.15 (O2)
unnamed: J16.5, U15.16 (O1)
unnamed: J17.2, U16.13 (O4)
unnamed: J17.3, U16.14 (O3)
unnamed: J17.4, U16.15 (O2)
unnamed: J17.5, U16.16 (O1)
unnamed: J18.2, U17.13 (O4)
unnamed: J18.3, U17.14 (O3)
unnamed: J18.4, U17.15 (O2)
unnamed: J18.5, U17.16 (O1)
unnamed: J19.2, U18.13 (O4)
unnamed: J19.3, U18.14 (O3)
unnamed: J19.4, U18.15 (O2)
unnamed: J19.5, U18.16 (O1)

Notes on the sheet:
Unipoloar Stepper Motor Drivers

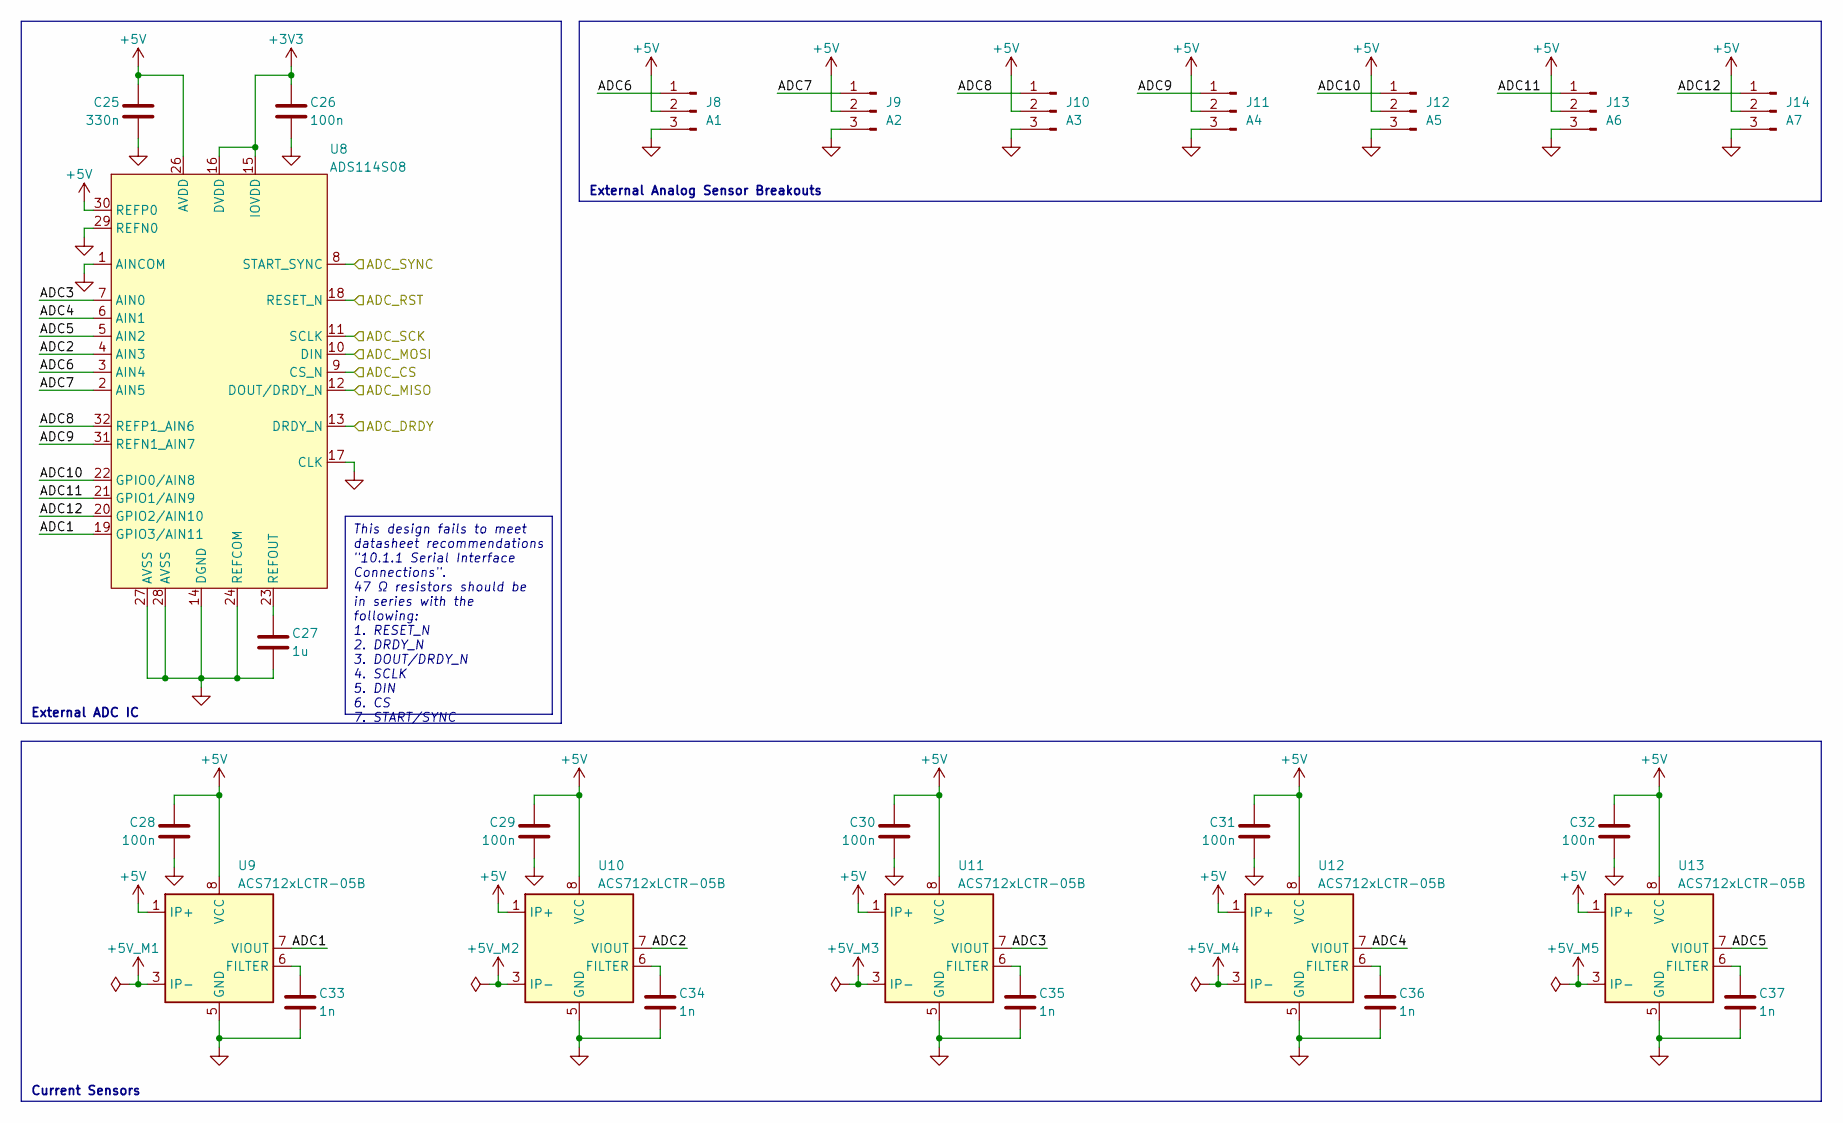
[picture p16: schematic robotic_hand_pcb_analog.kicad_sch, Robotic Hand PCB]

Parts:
C25: 330n; C_0603_1608Metric
C26, C28, C29, C30, C31, C32: 100n; C_0603_1608Metric
C27: 1u; C_0603_1608Metric
C33, C34, C35, C36, C37: 1n; C_0603_1608Metric
J8: A1; PinHeader_1x03_P2.54mm_Vertical
J9: A2; PinHeader_1x03_P2.54mm_Vertical
J10: A3; PinHeader_1x03_P2.54mm_Vertical
J11: A4; PinHeader_1x03_P2.54mm_Vertical
J12: A5; PinHeader_1x03_P2.54mm_Vertical
J13: A6; PinHeader_1x03_P2.54mm_Vertical
J14: A7; PinHeader_1x03_P2.54mm_Vertical
U8: ADS114S08; ads114s08_tqfp-32; Manufacturer Part Number ADS114S08
U9, U10, U11, U12, U13: ACS712xLCTR-05B; SOIC-8_3.9x4.9mm_P1.27mm

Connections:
+3V3: C26.2, U8.15 (IOVDD), U8.16 (DVDD); also elsewhere on the board
+5V: C25.2, C28.2, C29.2, C30.2, C31.2, C32.2, J8.2, J9.2, J10.2, J11.2, J12.2, J13.2, J14.2, U8.26 (AVDD), U8.30 (REFP0), U9.1 (IP+), U9.2 (IP+), U9.8 (VCC), U10.1 (IP+), U10.2 (IP+), U10.8 (VCC), U11.1 (IP+), U11.2 (IP+), U11.8 (VCC), U12.1 (IP+), U12.2 (IP+), U12.8 (VCC), U13.1 (IP+), U13.2 (IP+), U13.8 (VCC); also elsewhere on the board
+5V_M1: U9.3 (IP-), U9.4 (IP-); also elsewhere on the board
+5V_M2: U10.3 (IP-), U10.4 (IP-); also elsewhere on the board
+5V_M3: U11.3 (IP-), U11.4 (IP-); also elsewhere on the board
+5V_M4: U12.3 (IP-), U12.4 (IP-); also elsewhere on the board
+5V_M5: U13.3 (IP-), U13.4 (IP-); also elsewhere on the board
/EXTI2_ADC_DRDY: U8.13 (DRDY_N); also elsewhere on the board
/GPIO_ADC_RST: U8.18 (RESET_N); also elsewhere on the board
/GPIO_ADC_SYNC: U8.8 (START_SYNC); also elsewhere on the board
/GPIO_SPI3_CS: U8.9 (CS_N); also elsewhere on the board
/SPI3_MISO: U8.12 (DOUT/DRDY_N); also elsewhere on the board
/SPI3_MOSI: U8.10 (DIN); also elsewhere on the board
/SPI3_SCK: U8.11 (SCLK); also elsewhere on the board
/robotic_hand_pcb_analog/ADC1: U8.19 (GPIO3/AIN11), U9.7 (VIOUT)
/robotic_hand_pcb_analog/ADC2: U8.4 (AIN3), U10.7 (VIOUT)
/robotic_hand_pcb_analog/ADC3: U8.7 (AIN0), U11.7 (VIOUT)
/robotic_hand_pcb_analog/ADC4: U8.6 (AIN1), U12.7 (VIOUT)
/robotic_hand_pcb_analog/ADC5: U8.5 (AIN2), U13.7 (VIOUT)
/robotic_hand_pcb_analog/ADC6: J8.1, U8.3 (AIN4)
/robotic_hand_pcb_analog/ADC7: J9.1, U8.2 (AIN5)
/robotic_hand_pcb_analog/ADC8: J10.1, U8.32 (REFP1_AIN6)
/robotic_hand_pcb_analog/ADC9: J11.1, U8.31 (REFN1_AIN7)
/robotic_hand_pcb_analog/ADC10: J12.1, U8.22 (GPIO0/AIN8)
/robotic_hand_pcb_analog/ADC11: J13.1, U8.21 (GPIO1/AIN9)
/robotic_hand_pcb_analog/ADC12: J14.1, U8.20 (GPIO2/AIN10)
GND: C25.1, C26.1, C27.2, C28.1, C29.1, C30.1, C31.1, C32.1, C33.2, C34.2, C35.2, C36.2, C37.2, J8.3, J9.3, J10.3, J11.3, J12.3, J13.3, J14.3, U8.1 (AINCOM), U8.14 (DGND), U8.17 (CLK), U8.24 (REFCOM), U8.27 (AVSS), U8.28 (AVSS), U8.29 (REFN0), U9.5 (GND), U10.5 (GND), U11.5 (GND), U12.5 (GND), U13.5 (GND); also elsewhere on the board
unnamed: C27.1, U8.23 (REFOUT)
unnamed: C33.1, U9.6 (FILTER)
unnamed: C34.1, U10.6 (FILTER)
unnamed: C35.1, U11.6 (FILTER)
unnamed: C36.1, U12.6 (FILTER)
unnamed: C37.1, U13.6 (FILTER)

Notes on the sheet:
This design fails to meet datasheet recommendations "10.1.1 Serial Interface Connections". 47 Ω resistors should be in series with the following: 1. RESET_N 2. DRDY_N 3. DOUT/DRDY_N 4. SCLK 5. DIN 6. CS 7. START/SYNC
External Analog Sensor Breakouts
Current Sensors
External ADC IC

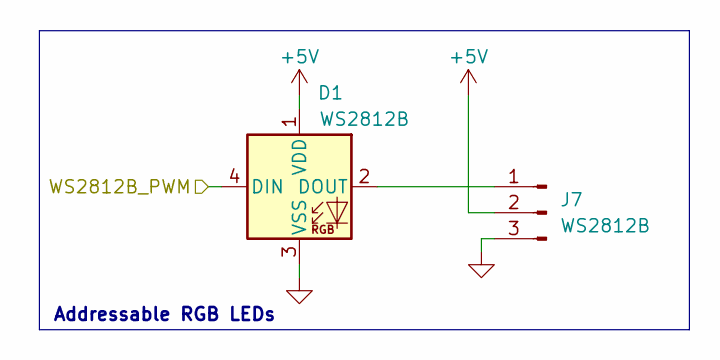
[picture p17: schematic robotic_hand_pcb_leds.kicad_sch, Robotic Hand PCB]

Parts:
D1: WS2812B; LED_WS2812B_PLCC4_5.0x5.0mm_P3.2mm
J7: WS2812B; PinHeader_1x03_P2.54mm_Vertical

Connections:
+5V: D1.1 (VDD), J7.2; also elsewhere on the board
/TIM1_CH1_PWM_{5V}: D1.4 (DIN); also elsewhere on the board
GND: D1.3 (VSS), J7.3; also elsewhere on the board
unnamed: D1.2 (DOUT), J7.1

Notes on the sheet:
Addressable RGB LEDs

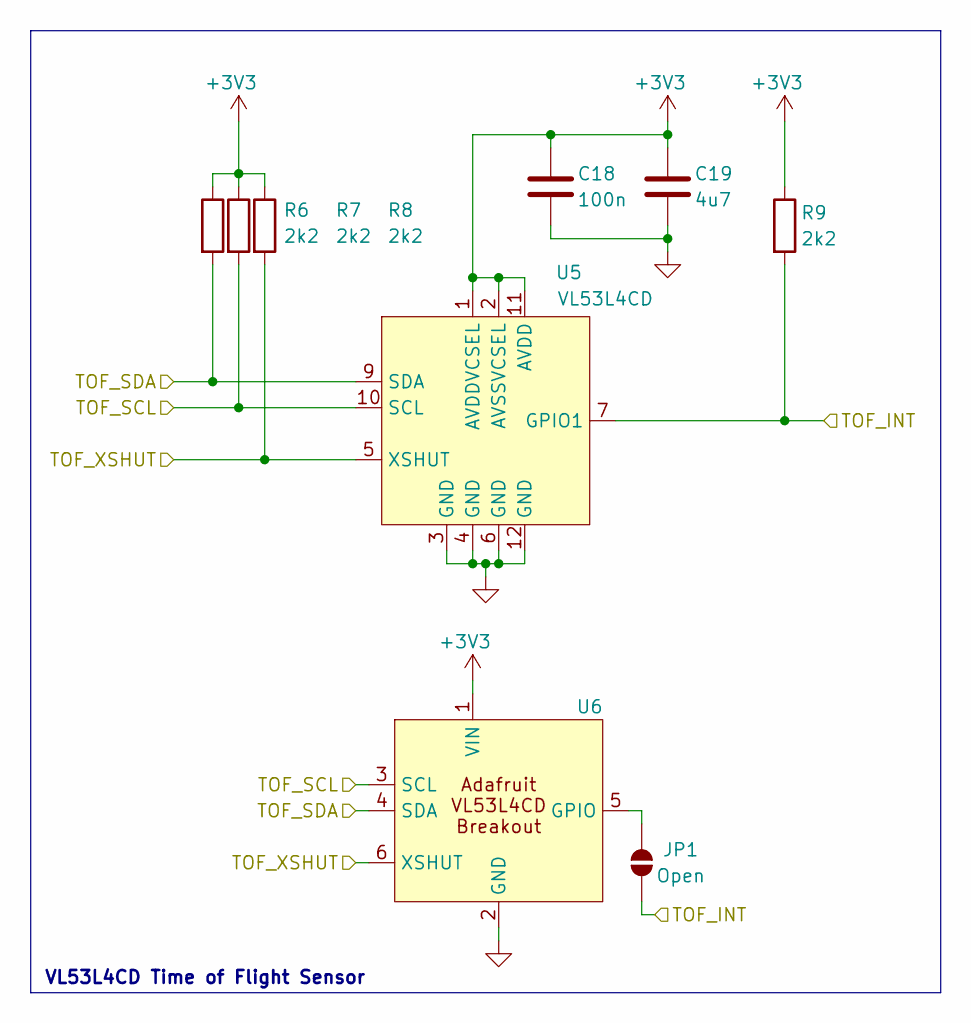
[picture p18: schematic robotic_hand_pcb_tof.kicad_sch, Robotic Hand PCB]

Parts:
C18: 100n; C_0603_1608Metric
C19: 4u7; C_0603_1608Metric
JP1: Open; SolderJumper-2_P1.3mm_Open_TrianglePad1.0x1.5mm
R6, R7, R8, R9: 2k2; R_0603_1608Metric
U5: VL53L4CD; vl53l4cd_lga12; Manufacturer Part Number VL53L4CDV0DH/1
U6: PinHeader_1x06_P2.54mm_Vertical; Manufacturer Part Number 5396

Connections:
+3V3: C18.1, C19.1, R6.1, R7.1, R8.1, R9.1, U5.1 (AVDDVCSEL), U5.2 (AVSSVCSEL), U5.11 (AVDD), U6.1 (VIN); also elsewhere on the board
/EXTI5_TOF_INT: JP1.1 (A), R9.2, U5.7 (GPIO1); also elsewhere on the board
/GPIO_TOF_XSHUT: R8.2, U5.5 (XSHUT), U6.6 (XSHUT); also elsewhere on the board
/I2C1_SCL: R7.2, U5.10 (SCL), U6.3 (SCL); also elsewhere on the board
/I2C1_SDA: R6.2, U5.9 (SDA), U6.4 (SDA); also elsewhere on the board
GND: C18.2, C19.2, U5.3 (GND), U5.4 (GND), U5.6 (GND), U5.12 (GND), U6.2 (GND); also elsewhere on the board
unnamed: JP1.2 (B), U6.5 (GPIO)

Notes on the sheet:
VL53L4CD Time of Flight Sensor

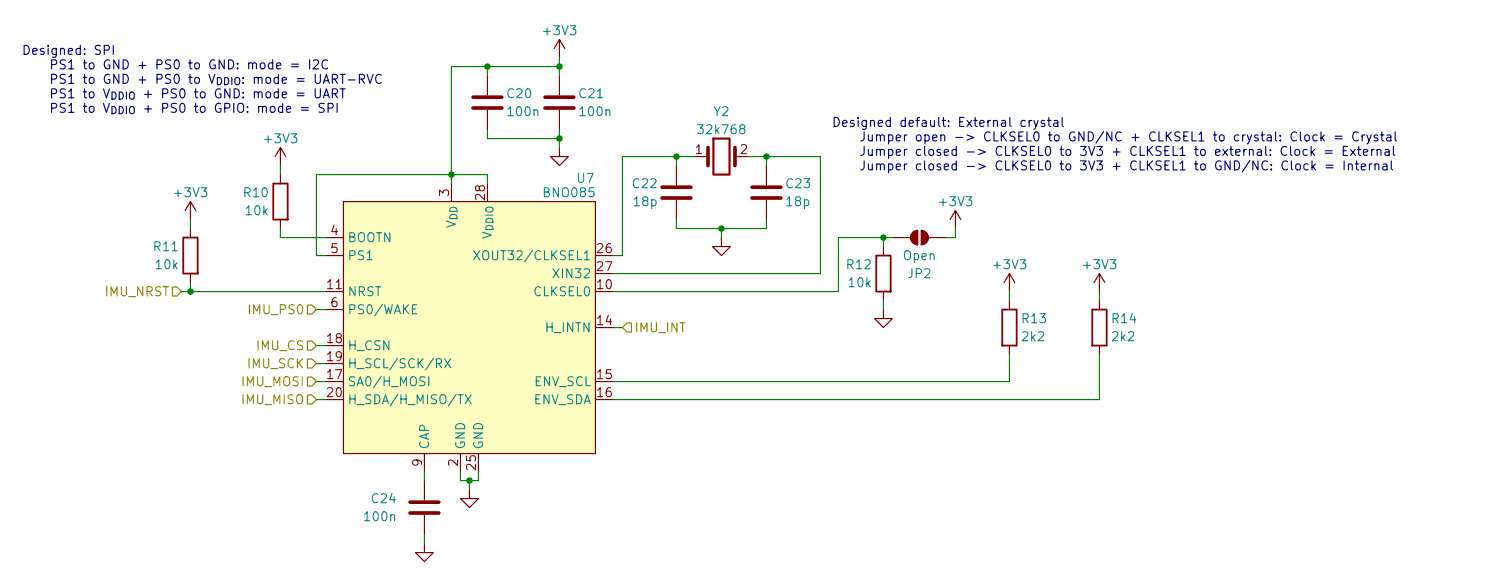
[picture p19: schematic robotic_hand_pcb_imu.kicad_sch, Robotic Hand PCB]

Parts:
C20, C21, C24: 100n; C_0603_1608Metric
C22, C23: 18p; C_0402_1005Metric
JP2: Open; SolderJumper-2_P1.3mm_Open_TrianglePad1.0x1.5mm
R10, R11, R12: 10k; R_0603_1608Metric
R13, R14: 2k2; R_0603_1608Metric
U7: BNO085; bno085; Manufacturer Part Number BNO085
Y2: 32k768; ecs_ecx-34r; Manufacturer Part Number ECS-.327-12.5-34R-C-TR

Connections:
+3V3: C20.1, C21.1, JP2.2 (B), R10.1, R11.1, R13.1, R14.1, U7.3 (V_{DD}), U7.5 (PS1), U7.28 (V_{DDIO}); also elsewhere on the board
/EXTI4_IMU_INT: U7.14 (H_INTN); also elsewhere on the board
/GPIO_IMU_P0: U7.6 (PS0/WAKE); also elsewhere on the board
/GPIO_IMU_RST: R11.2, U7.11 (NRST); also elsewhere on the board
/GPIO_SPI1_CS: U7.18 (H_CSN); also elsewhere on the board
/SPI1_MISO: U7.20 (H_SDA/H_MISO/TX); also elsewhere on the board
/SPI1_MOSI: U7.17 (SA0/H_MOSI); also elsewhere on the board
/SPI1_SCK: U7.19 (H_SCL/SCK/RX); also elsewhere on the board
GND: C20.2, C21.2, C22.2, C23.2, C24.2, R12.2, U7.2 (GND), U7.25 (GND); also elsewhere on the board
unnamed: JP2.1 (A), R12.1, U7.10 (CLKSEL0)
unnamed: R10.2, U7.4 (BOOTN)
unnamed: C24.1, U7.9 (CAP)
unnamed: R13.2, U7.15 (ENV_SCL)
unnamed: R14.2, U7.16 (ENV_SDA)
unnamed: C23.1, U7.27 (XIN32), Y2.2
unnamed: C22.1, U7.26 (XOUT32/CLKSEL1), Y2.1

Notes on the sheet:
Designed: SPI PS1 to GND + PS0 to GND: mode = I2C PS1 to GND + PS0 to V_{DDIO}: mode = UART-RVC PS1 to V_{DDIO} + PS0 to GND: mode = UART PS1 to V_{DDIO} + PS0 to GPIO: mode = SPI
Designed default: External crystal Jumper open -> CLKSEL0 to GND/NC + CLKSEL1 to crystal: Clock = Crystal Jumper closed -> CLKSEL0 to 3V3 + CLKSEL1 to external: Clock = External Jumper closed -> CLKSEL0 to 3V3 + CLKSEL1 to GND/NC: Clock = Internal

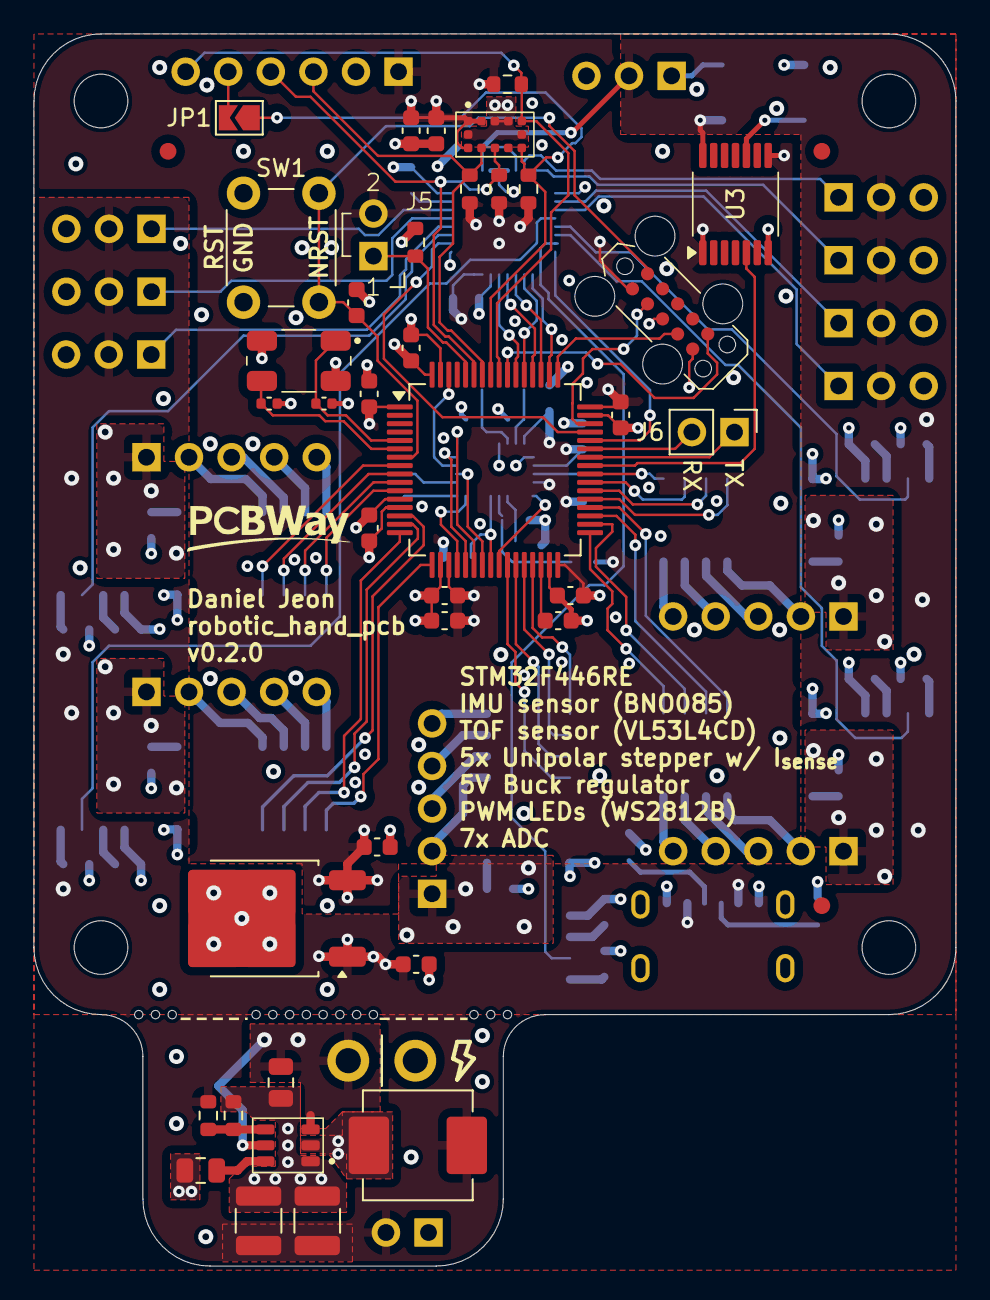
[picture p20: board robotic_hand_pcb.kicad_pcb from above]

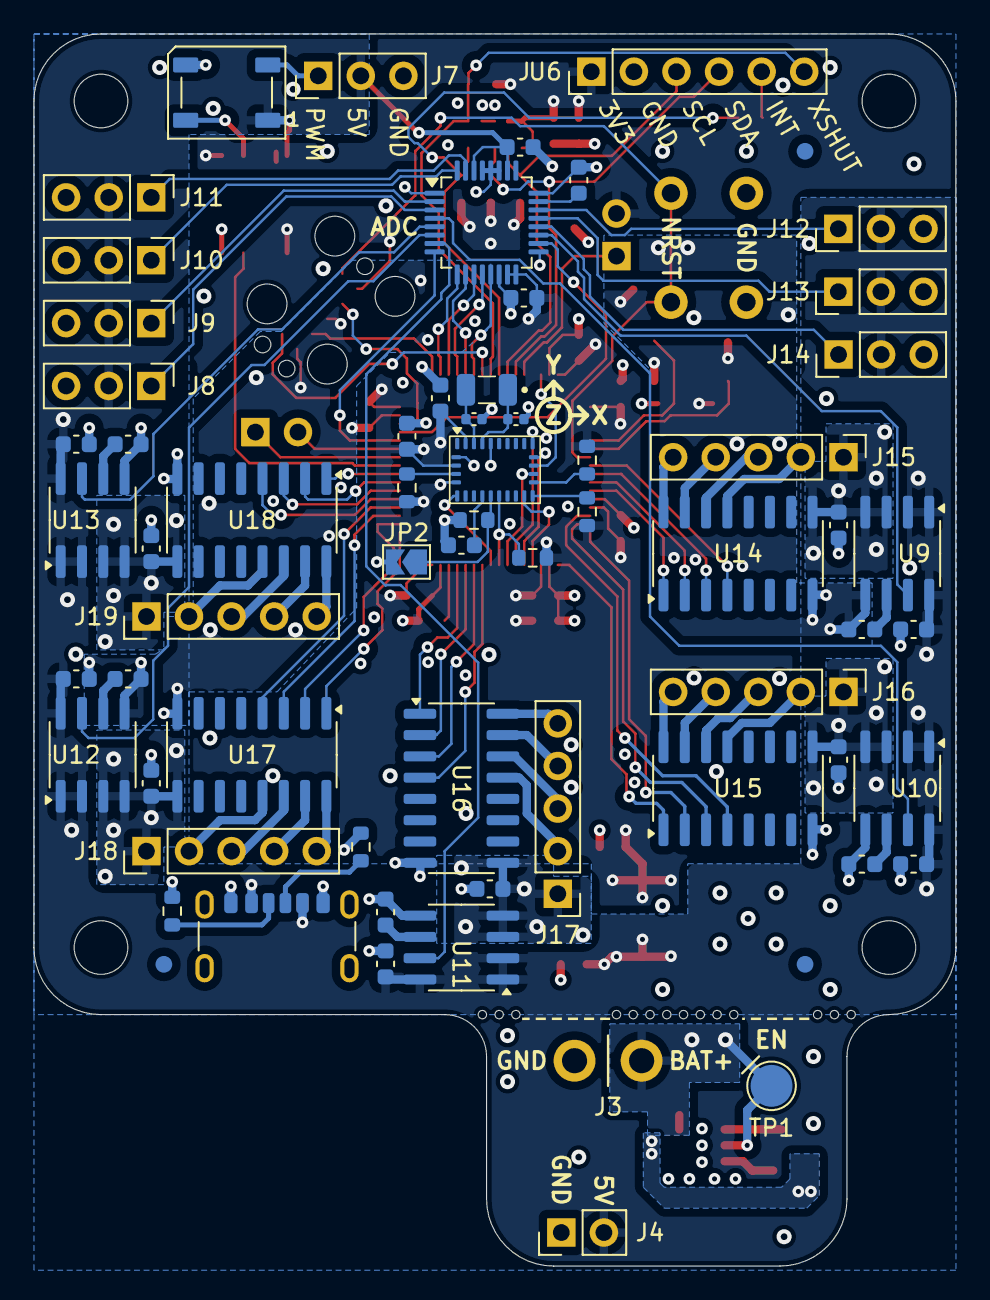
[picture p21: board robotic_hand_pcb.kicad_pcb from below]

Board: 4 copper layers, 55.0 x 73.5 mm, 111 parts (66 on the bottom side), 111 nets.

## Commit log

2025-02-21 Recover WIP following branch nuke
    [robotic_hand_pcb.kicad_pcb, robotic_hand_pcb.kicad_sch, robotic_hand_pcb_imu.kicad_sch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]
2025-02-21 Add 5V buck regulator
    [robotic_hand_pcb.kicad_sch, robotic_hand_pcb_imu.kicad_sch, robotic_hand_pcb_leds.kicad_sch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]
2025-02-21 Pass ERC
    [robotic_hand_pcb.kicad_sch, robotic_hand_pcb_leds.kicad_sch, robotic_hand_pcb_servos.kicad_sch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]
2025-02-21 Update for WIP changes
    [robotic_hand_pcb.kicad_sch, robotic_hand_pcb_analog.kicad_sch, robotic_hand_pcb_imu.kicad_sch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]
2025-02-21 Update symbol and footprint tables
2025-02-21 Add WIP schematic changes
    [robotic_hand_pcb.kicad_sch, robotic_hand_pcb_analog.kicad_sch, robotic_hand_pcb_imu.kicad_sch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]
2025-02-21 Pass ERC, update component_library
    [robotic_hand_pcb_analog.kicad_sch, robotic_hand_pcb_imu.kicad_sch, robotic_hand_pcb_tof.kicad_sch]
2025-02-21 Assign footprints
    [robotic_hand_pcb.kicad_sch, robotic_hand_pcb_analog.kicad_sch, robotic_hand_pcb_leds.kicad_sch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]
2025-02-21 Fix symbol error, update component_library
    [robotic_hand_pcb.kicad_pcb, robotic_hand_pcb_tof.kicad_sch]
2025-02-21 Cleanup and remove unneeded connectors
    [robotic_hand_pcb_analog.kicad_sch, robotic_hand_pcb_tof.kicad_sch, robotic_hand_pcb_unipolar_steppers.kicad_sch]
2025-02-21 Add WIP PCB layout and routing
    [robotic_hand_pcb.kicad_pcb, robotic_hand_pcb.kicad_sch, robotic_hand_pcb_analog.kicad_sch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]
2025-02-21 Swap adafruit breakout for pin header footprint
    [robotic_hand_pcb.kicad_pcb, robotic_hand_pcb_tof.kicad_sch]
2025-02-21 Update WIP, clean up stepper drivers
    [robotic_hand_pcb.kicad_pcb, robotic_hand_pcb.kicad_sch, robotic_hand_pcb_analog.kicad_sch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]
2025-02-21 Cleanup layout, add WIP routing
    [robotic_hand_pcb.kicad_pcb, robotic_hand_pcb.kicad_sch, robotic_hand_pcb_analog.kicad_sch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]
2025-02-21 Add minor layout improvements
    [robotic_hand_pcb.kicad_pcb]
2025-02-21 Route power, add major cleanup
    [robotic_hand_pcb.kicad_pcb, robotic_hand_pcb.kicad_sch, robotic_hand_pcb_analog.kicad_sch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]
2025-02-21 Near complete routing, cleanup
    [robotic_hand_pcb.kicad_pcb, robotic_hand_pcb.kicad_sch, robotic_hand_pcb_analog.kicad_sch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]
2025-02-21 Cleanup silkscreen
    [robotic_hand_pcb.kicad_pcb]
2025-02-21 Add WIP ADC routes
    [robotic_hand_pcb.kicad_pcb, robotic_hand_pcb.kicad_sch, robotic_hand_pcb_analog.kicad_sch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]
2025-02-21 Add WIP ADC and TOF routing
    [robotic_hand_pcb.kicad_pcb]
2025-02-21 Add initial board spec tables
2025-02-21 Add WIP buck converter layout
    [robotic_hand_pcb.kicad_pcb]
2025-02-21 Initial full PCB design, pass DRC
    [IHLP2525CZ.step, robotic_hand_pcb.kicad_pcb, robotic_hand_pcb.kicad_sch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]
2025-02-21 Fill empty spaces with GND pour
    [robotic_hand_pcb.kicad_pcb]
2025-02-21 Add stitching vias and final touches
    [robotic_hand_pcb.kicad_pcb]
2025-02-22 Cleanup and update docs
    [robotic_hand_pcb.kicad_pcb]
2025-02-22 Add PCBWay logo silkscreen
    [robotic_hand_pcb.kicad_pcb]
2025-02-22 Fix conflicting GPIO EXTI4 usage
    [robotic_hand_pcb.kicad_pcb, robotic_hand_pcb.kicad_sch]
2025-02-26 Fix C4 value error and cleanup silkscreen
    [robotic_hand_pcb.kicad_pcb, robotic_hand_pcb.kicad_sch, robotic_hand_pcb_analog.kicad_sch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]
2025-02-26 Update revision number
    [robotic_hand_pcb.kicad_pcb, robotic_hand_pcb.kicad_sch, robotic_hand_pcb_analog.kicad_sch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]
2025-03-05 Add v0.1.0 assembly pictures
2025-03-17 Fix ADC IC decoupling
    [robotic_hand_pcb.kicad_pcb, robotic_hand_pcb_analog.kicad_sch]
2025-03-17 Utilize AINCOM
    [robotic_hand_pcb.kicad_pcb, robotic_hand_pcb_analog.kicad_sch]
2025-03-17 Add documentation related to issue #2
    [robotic_hand_pcb_analog.kicad_sch]
2025-03-19 Add battery connector README docs
2025-03-24 Update PCB for ADS114S08 rework fixes, v0.2.0
    [robotic_hand_pcb.kicad_pcb, robotic_hand_pcb.kicad_sch, robotic_hand_pcb_analog.kicad_sch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]
